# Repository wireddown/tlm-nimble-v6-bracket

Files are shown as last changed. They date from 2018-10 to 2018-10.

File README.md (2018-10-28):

# TLM Nimble V6 Bracket

Zesty Technology designed a [Nimble](https://zestytechnology.readthedocs.io/en/latest/nimble/index.html) mounting [bracket](https://www.thingiverse.com/thing:2701541) for [Tevo](https://tevo3dprinterstore.com) Little Monster 3D printers with the stock effector and hotend. This is an update for effectors with the [E3D V6](https://e3d-online.dozuki.com/Guide/V6+Assembly/6) + [Volcano](https://e3d-online.dozuki.com/Guide/Building+a+new+Volcano/9) hotend.

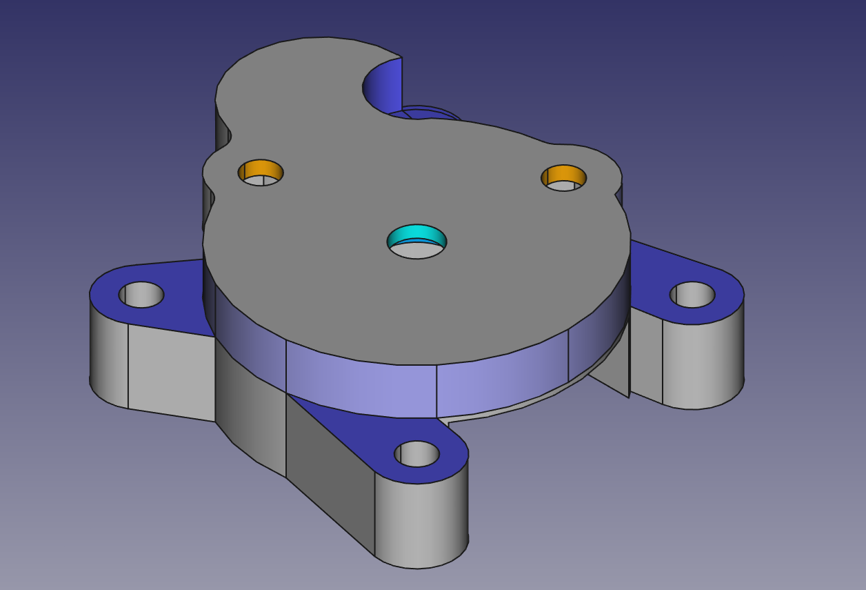
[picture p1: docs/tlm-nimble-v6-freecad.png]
rendering of the updated bracket


* [Base plate](/docs/tlm-nimble-v6-base-plate-freecad.stl) stl
* [Position plate](/docs/tlm-nimble-v6-position-plate-freecad.stl) stl

## Summary of changes

1. Enlarged the through-hole to allow the PTFE feed tube to pass
   - Otherwise, the filament would be free to bend/kink in the 10 mm gap between bottom of the Nimble and the top of the V6.
1. Removed material that blocked the tube collet and collet clip
   - Otherwise, the bracket would not sit flush on the effector.
1. Deepened the Nimble bolt countersinks
   - Otherwise, the bolts would strike the bottom and split the bracket in two during installation.
1. Lowered the surface for the effector mounting holes
   - Purely cosmetic, and allows for shorter mounting bolts when attaching the bracket to the effector in trade for printing some equivalent support material.

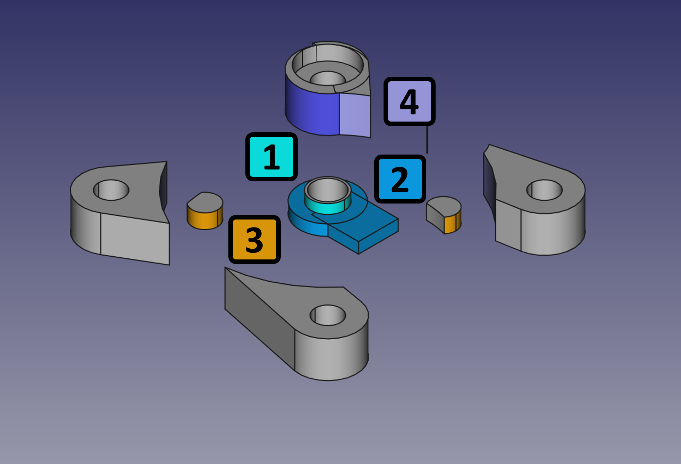
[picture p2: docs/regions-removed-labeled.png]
rendering of the removed regions from the original bracket


### Demo part showing 10 mm gap

photo comparison showing 10 mm gap

## Size: 1.75 mm filament models

E3D has both 1.75 mm and 3 mm sized models of their V6 hotend, and this bracket has been designed for the 1.75 mm variants.

If you have a 3 mm V6 and want to use the Nimble with your TLM, open an issue!

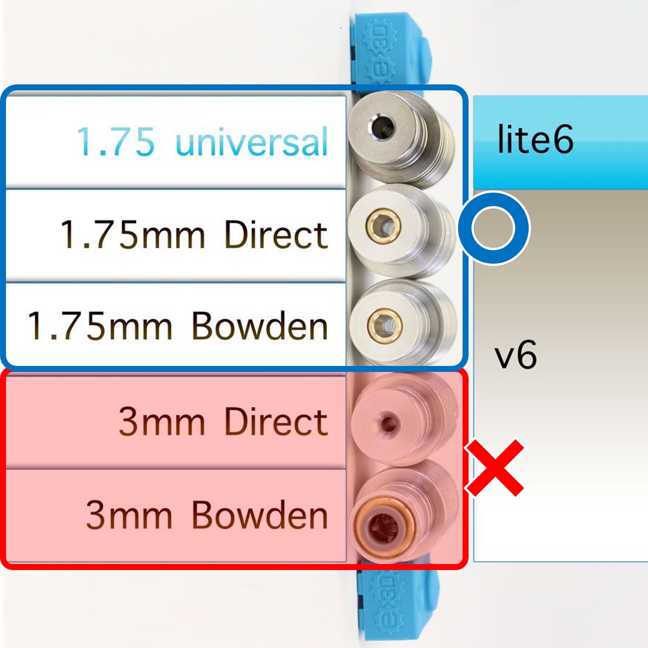
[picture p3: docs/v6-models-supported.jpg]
V6 model sizes


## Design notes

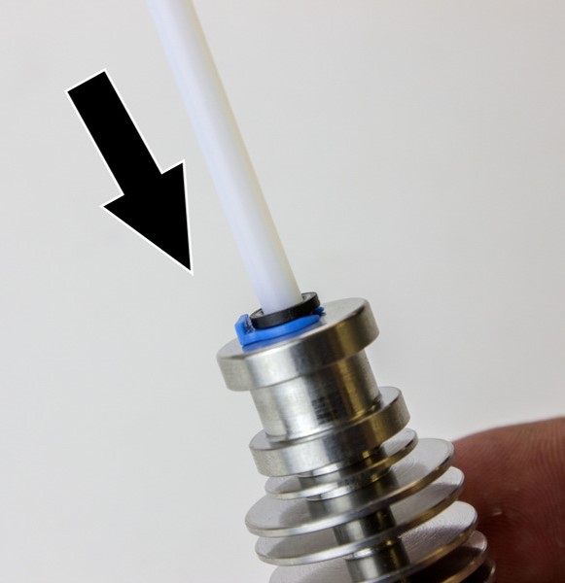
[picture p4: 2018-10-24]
docs/v6-top-end.jpg

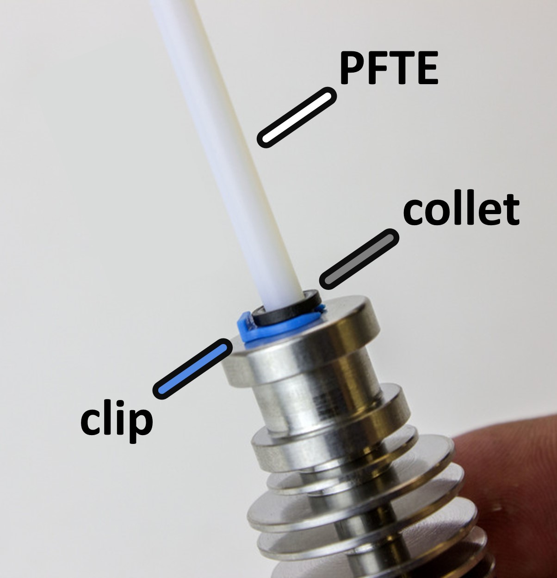
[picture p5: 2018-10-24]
docs/v6-top-end-labeled.jpg

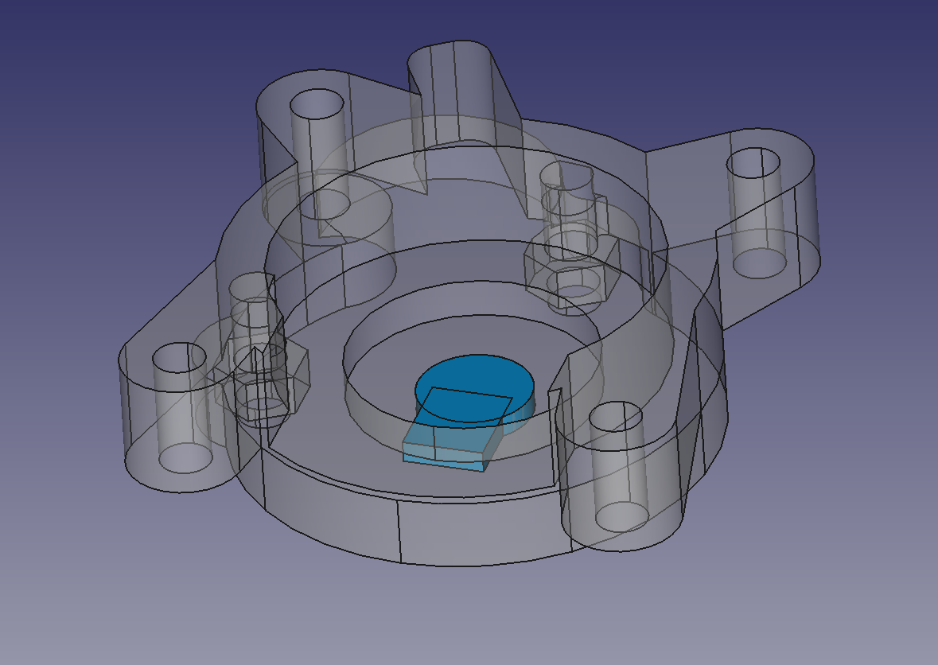
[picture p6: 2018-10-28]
docs/collet-clearance-bottom.png

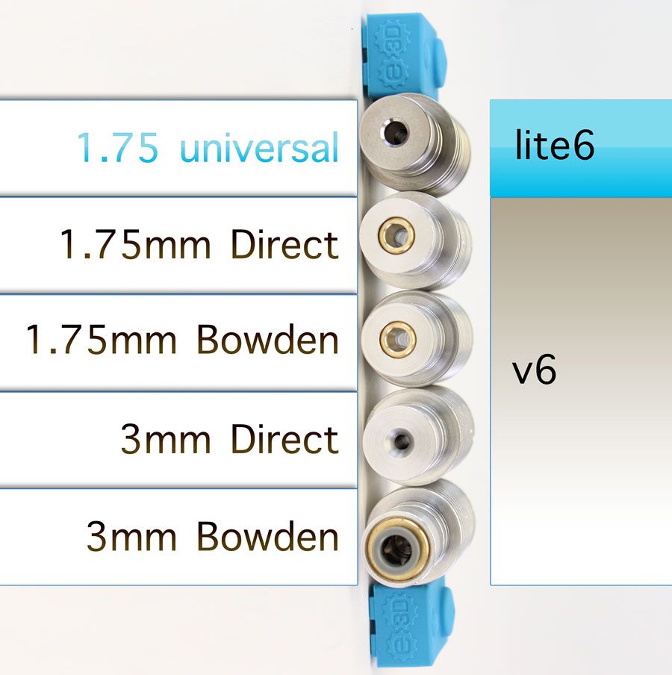
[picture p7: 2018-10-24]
docs/v6-models.jpg

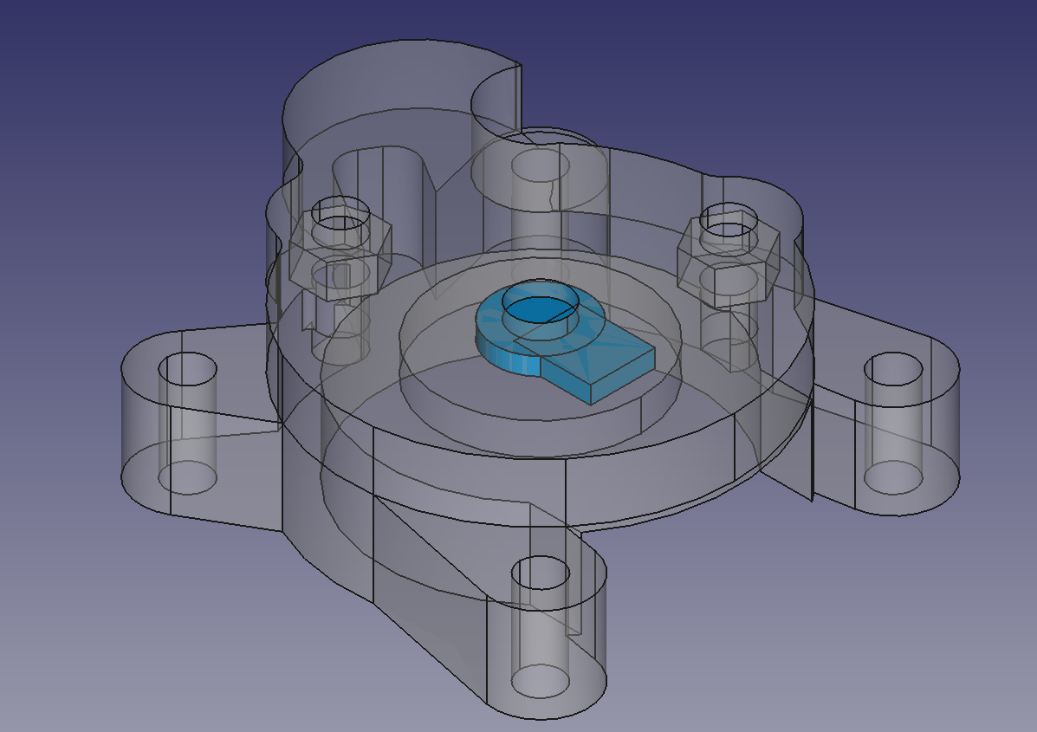
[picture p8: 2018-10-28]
docs/collet-clearance.png

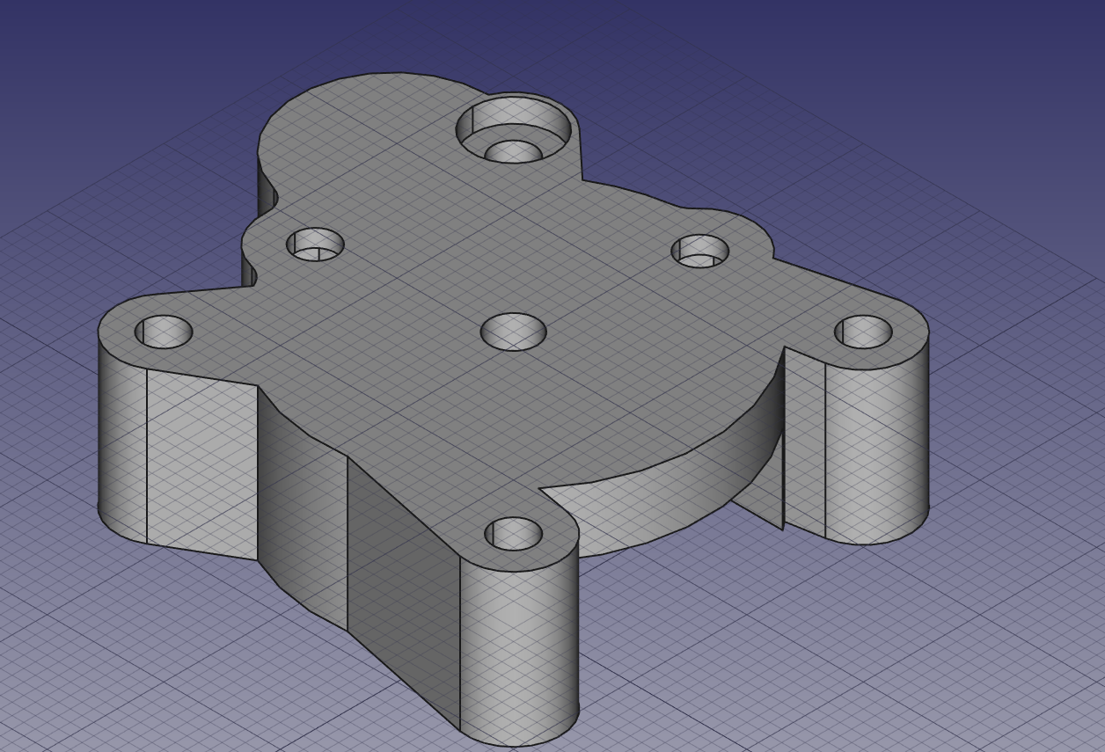
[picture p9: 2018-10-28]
docs/original-nimble-bracket.png

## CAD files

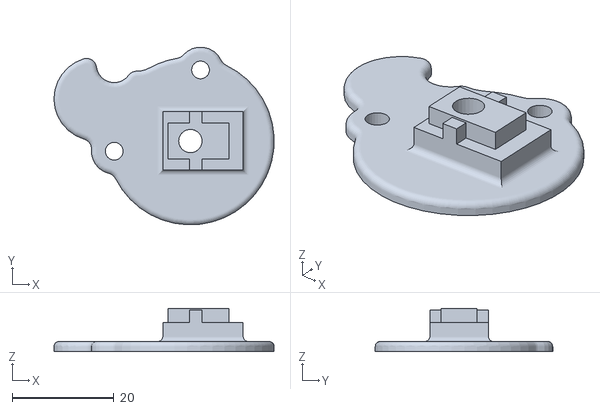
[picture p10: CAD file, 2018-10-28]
docs/tlm-nimble-v6-position-plate-freecad.stl
43.3 x 35.0 x 8.52

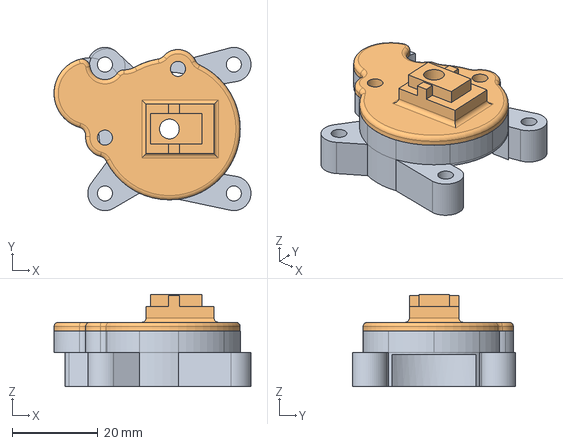
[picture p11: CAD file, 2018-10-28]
src/freecad/tlm-nimble-v6-freecad.FCStd
45.9 x 38.0 x 21.5 mm
tlm-nimble-v6-bracket
tlm-nimble-v6-position-plate

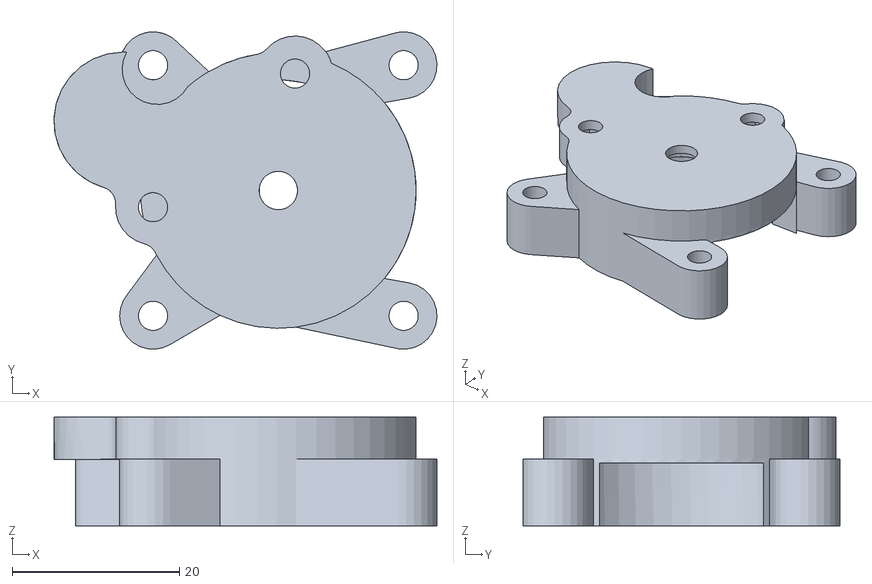
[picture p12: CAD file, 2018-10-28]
docs/tlm-nimble-v6-base-plate-freecad.stl
45.9 x 38.0 x 13.0

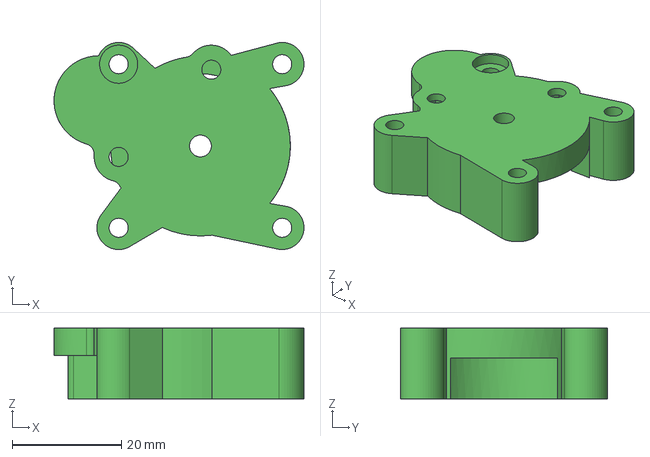
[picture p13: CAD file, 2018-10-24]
upstream/Base_Mount_V1.1.stp
45.9 x 38.0 x 13.0 mm

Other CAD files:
upstream/Position_plate_V1.1.stp

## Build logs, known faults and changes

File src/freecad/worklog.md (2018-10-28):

# Work log

## Tools and environment

* FreeCAD 0.17 (released August 2018)
* Windows 10

## Approach

Because Zesty provided a solid shape in a STEP-file, I used the Part Workbench and cut into the shape with boolean operations. I chose against both Part Design and Sketcher because there weren't any drawings of any of the faces. I'm curious about the Reverse Engineering Workbench and using it to extract dimensions and constraints, but I chose the naïve brute-force approach to minimize surprises.

### Add the base parts

From the Part menu, I selected "Import CAD..."

### Enlarge the through-hole to allow the PTFE feed tube to pass
Otherwise, the filament can bend/kink in the 10 mm gap between bottom of the Nimble and the top of the V6.

One shape to cut:

* a cylinder: 2.3 mm r x 2.8 mm

Use this shape on the both the mount base and position plate to widen the PTFE tube hole.

### Remove material that blocks the tube collet and collet clip
Otherwise, the bracket does not sit flush on the effector.

Two shapes to cut:

* a cube: 6.5 mm x 5.5 mm x 1.5 mm
* a cylinder: 3.9 mm r x 1.5 mm

Place them flush to the same plane on their flat sides. Align their center axes and move them until they join. When their combined length is 11 mm, fuse them into one shape. Center the circle with the center of the through-hole and with the cube pointing towards the wide opening on the side of the base bracket. Finally, move the object Z-wise so that cube is flush with inner tier and cut the shape from the bracket.

### Deepen the Nimble bolt countersinks
Otherwise, the bolts strike the bottom and split the bracket in two during installation.

One shape to cut, twice:

* a cylinder: 1.75 mm r x 10 mm

Position these so that they are centered over the Nimble mounting bolt counter sinks. Lower them into the base bracket until the top of the cylinders are flush with the top face and cut them from the bracket.

### Lower the surface for the effector mounting holes
Purely cosmetic, and allows for shorter mounting bolts when attaching the bracket to the effector.

Many shapes to cut:

* a cube: 40 mm x 40 mm x 5 mm
* a cylinder, twice: 4.8 mm r x 5 mm
* a cylinder: 16.5 mm r x 5 mm
* a cylinder: 8.3 mm r x 5 mm
* a cube: 18.1 mm x 15 mm x 5 mm
* a cylinder: 4.2 mm r x 5 mm

The first cube is the main shape used to cut the mount. To quickly make the cutting shape, center the large cube over the base bracket's filament hole and lower it 2 mm below the top face of the bracket. To keep the core of the mount, the bolt stops, and gear housing, place the remaining pieces, except for the last cylinder, so that they are flush with the top face of the bracket and arrange them so they overlap those critical regions. Then, fuse them together before cutting the resulting shape from large cube. Finally, place the last cylinder so that it cuts the mounting face for the bolt beneath the Nimble flush and fuse it with the remainder of the large cube. Cut this final shape from the Nimble base shape to complete the updates.

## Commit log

2018-10-24 Introducing the TLM Nimble-Volcano bracket
    This is an update for effectors with the E3D V6 + Volcano hotend
2018-10-24 Add upstream source files
    These files are from ZestyTech's Mount for Nimble on Tevo Little Monster
    https://www.thingiverse.com/thing:2701541/files
    Licensed under the Creative Commons - Attribution license.
    [Base_Mount_V1.1.stp, Position_plate_V1.1.stp]
2018-10-24 Add the base part
    via Part menu » Import CAD... dialog
2018-10-24 Shelve for the day
    * Add dimensions for basic cuts
    * Create shapes for basic cuts
    WIP: begin modeling the cosmetic cut
    [tlm-nimble-v6-freecad.FCStd]
2018-10-25 Add the final shoulder cut shape
    Also describe that process
    [tlm-nimble-v6-freecad.FCStd]
2018-10-25 Tidy and correct dimensions
    [tlm-nimble-v6-freecad.FCStd]
2018-10-25 Fix: keep curve segment connecting mount bolt to the core
    "Missed a spot" found when I made an intersection of the part and the cutting shape: I saw a connecting curve incorrectly being removed.
    Adjusted a few dimensions and positions to match.
    [tlm-nimble-v6-freecad.FCStd]
2018-10-25 Completed FreeCAD design for tlm-nimble-v6
    * Final dimension adjustments
    * Add screenshots of base, negative, final models
    * Add mesh file
    [tlm-nimble-v6-freecad.FCStd, tlm-nimble-v6-freecad.stl]
2018-10-26 Major fix: the 4th mount bolt face wasn't flush
    So make it flush by fusing another cylinder to the should cut.
    Update the dimensions and instructions to match.
    [tlm-nimble-v6-freecad.FCStd, tlm-nimble-v6-freecad.stl]
2018-10-26 Add the position plate
    Polish the work log too
    [tlm-nimble-v6-base-plate-freecad.stl, tlm-nimble-v6-freecad.FCStd, tlm-nimble-v6-position-plate-freecad.stl]
2018-10-26 Fix URL typos to stl files
2018-10-26 Remove STL file location
2018-10-26 Add links to stl files
2018-10-27 Add illustrations of internal cuts
    collet-clearance-*.png show where the cut to make room for the collet needs to be
    ptfe-tube-clearance.png shows the 10 mm span where the filament might bend/kink
    Creating the illustrations uncovered an incorrect dimension for the PTFE cut on the position plate. Fixed the drawing and re-exported the stl.
    [tlm-nimble-v6-freecad.FCStd, tlm-nimble-v6-position-plate-freecad.stl]
2018-10-28 Attempt at showing the 10 mm gap
2018-10-28 Fix link to stl files
